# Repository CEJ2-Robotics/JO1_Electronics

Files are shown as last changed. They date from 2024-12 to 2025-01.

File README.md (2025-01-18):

# John Deere Tractor Navigation System - Electronics

<p align="justify"> This repository contains the PCB layout for a <strong>shield-style board</strong> designed to interface with the <i>NUCLEO-H745ZI-Q</i> development board. The PCB integrates various components and connection interfaces required for the tractor navigation system developed in collaboration with John Deere, serving as a practical application of embedded systems concepts. The implementation details of this electronics design can be found in the <a href="https://github.com/CEJ2-Robotics/JO1_Embedded">embedded software repository</a>.</p>

<p align="center">
  PCB 3D View
</p>

<p align="center">
  PCB Layout
</p>

## System Overview

<p align="justify">The custom PCB serves as a connection hub for the system's components, handling:</p>

<ul>
  <li><strong>Power distribution</strong> to components</li>
  <li><strong>CAN interface (FDCAN1)</strong> for encoder data</li>
  <li><strong>I2C connection (I2C4)</strong> for the MPU6050 IMU</li>
  <li><strong>SPI interface (SPI5)</strong> for the nRF24L01 wireless module</li>
  <li><strong>PWM signal routing (TIM13, TIM14, TIM1)</strong> for motors and buzzer</li>
</ul>

## Power Distribution

<p align="justify">The PCB design includes three power input screw terminals. Here's our implementation from the embedded repository:</p>

### Logic Power Screw Terminals

<ul>
  <li><strong>5V terminal:</strong> Connected to external LM2596 regulator outputting 5V</li>
  <li><strong>3.3V terminal:</strong> Connected to external LM2596 regulator outputting 3.3V</li>
  <li>Both regulators were powered by 7.4V from two <strong>3.7V Li-Po cells</strong> in series</li>
</ul>

### STM32 Power Screw Terminal

<ul>
  <li><strong>7.4V terminal:</strong> Connects directly to NUCLEO-H745ZI-Q's VIN</li>
  <li><strong>Board configuration:</strong> JP2 jumper on pins 3-4</li>
  <li><strong>Power specifications:</strong>
    <ul>
      <li><strong>Input range:</strong> 7-11V</li>
      <li><strong>Current draw varies with voltage:</strong></li>
      <ul>
        <li>800mA @ 7V</li>
        <li>450mA @ 7-9V</li>
        <li>250mA @ 9-11V</li>
      </ul>
    </ul>
  </li>
</ul>

<p align="center">
  STM32 Power Supply Input from VIN
</p>

### ESC and STM32 Connection

<ul>
  <li>The <strong>ESC</strong> is a separate pre-built circuit with its own power connections and is not powered through the PCB.</li>
  <li>In our setup, we used a <strong>7.4V Li-Po 2S battery</strong> to power both:
    <ul>
      <li>The <strong>ESC</strong> directly</li>
      <li>The <strong>STM32</strong> through the PCB's 7.4V screw terminal</li>
    </ul>
  </li>
</ul>

## Schematic Diagram & Component List

<p align="center">
  Schematic Diagram
</p>

| Component | Specifications | Purpose | Location |
|--- |--- |--- |--- |
| NUCLEO-H745ZI-Q | Dual-core ARM Cortex-M7/M4  | Main controller | Shield base board |
| Arduino Nano | ATmega328P | Encoder preprocessing | On shield PCB |
| nRF24L01 | 2.4GHz wireless module | GPS data reception | On shield PCB |
| MPU6050 | 6-DOF IMU | Orientation tracking | On shield PCB |
| GM 25-370 | 12V DC motor with encoder | Drive system | External (pins on PCB) |
| MCP2515 | CAN controller | CAN-SPI interface | On shield PCB |
| TJA1051 | CAN transceiver | CAN physical layer | On shield PCB |
| MG996R | Servo motor | Steering control | External (pins on PCB) | 
| 30A ESC | Electronic speed controller | Motor drive control | External (pins on PCB) |
| HW-508 | Passive buzzer | Audio feedback | On shield PCB |
| LM2596 (x2) | DC-DC Step Down | 5V and 3.3V regulation | External (recommended) |

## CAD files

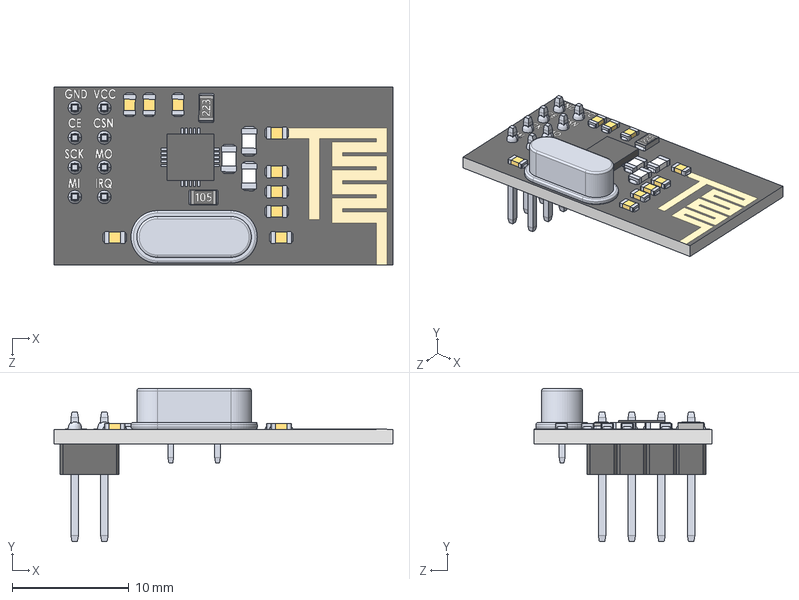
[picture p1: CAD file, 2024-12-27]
JO1_PCB/COMPONENTS/3D/NRF24L01.STEP
29.0 x 13.1 x 15.2 mm
nrfboard
CrystalOscillator
doubleMaleHeader x 4
solder x 8
1.7mmSmdCeramicCapacitor x 9
smdResistor223
smdResistor105
smdceramiccapacitorwhite x 3
4x4SMDchip

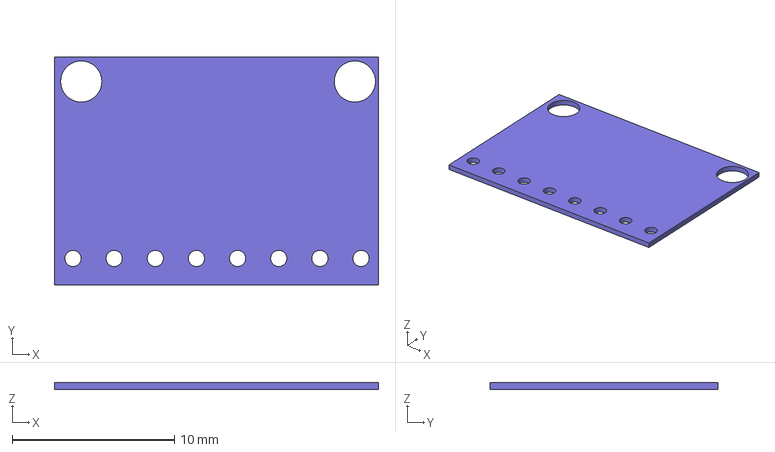
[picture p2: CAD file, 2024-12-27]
JO1_PCB/COMPONENTS/3D/TJA1051.step
20.0 x 14.1 x 0.411 mm

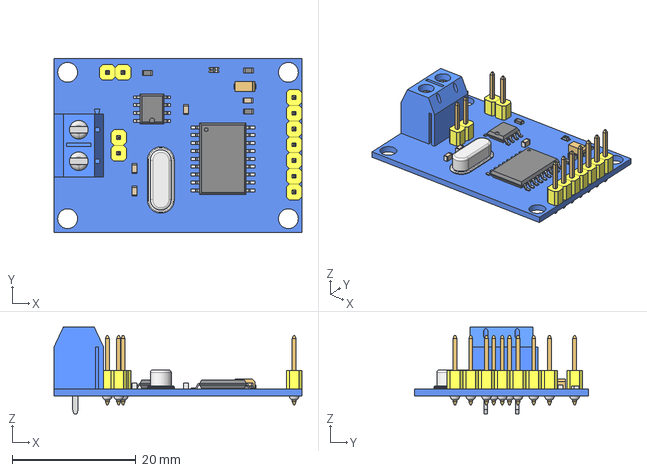
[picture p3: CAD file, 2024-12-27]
JO1_PCB/COMPONENTS/3D/MCP2515.step
40.0 x 28.0 x 14.0 mm

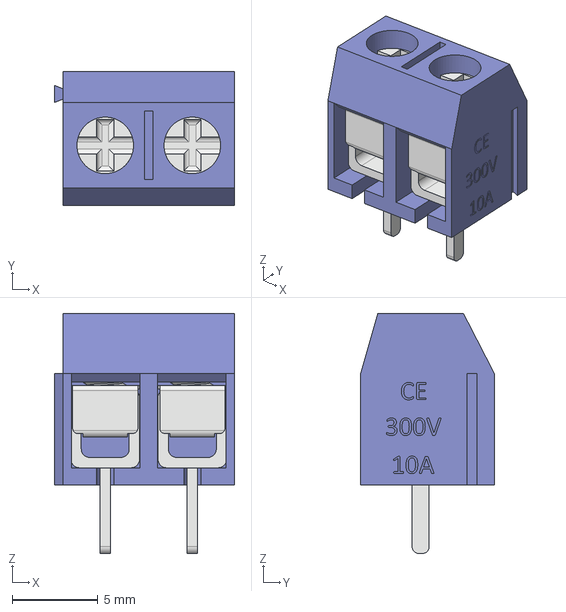
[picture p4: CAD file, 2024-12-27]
JO1_PCB/COMPONENTS/3D/SCREW_TERMINAL.step
10.5 x 7.80 x 14.0 mm

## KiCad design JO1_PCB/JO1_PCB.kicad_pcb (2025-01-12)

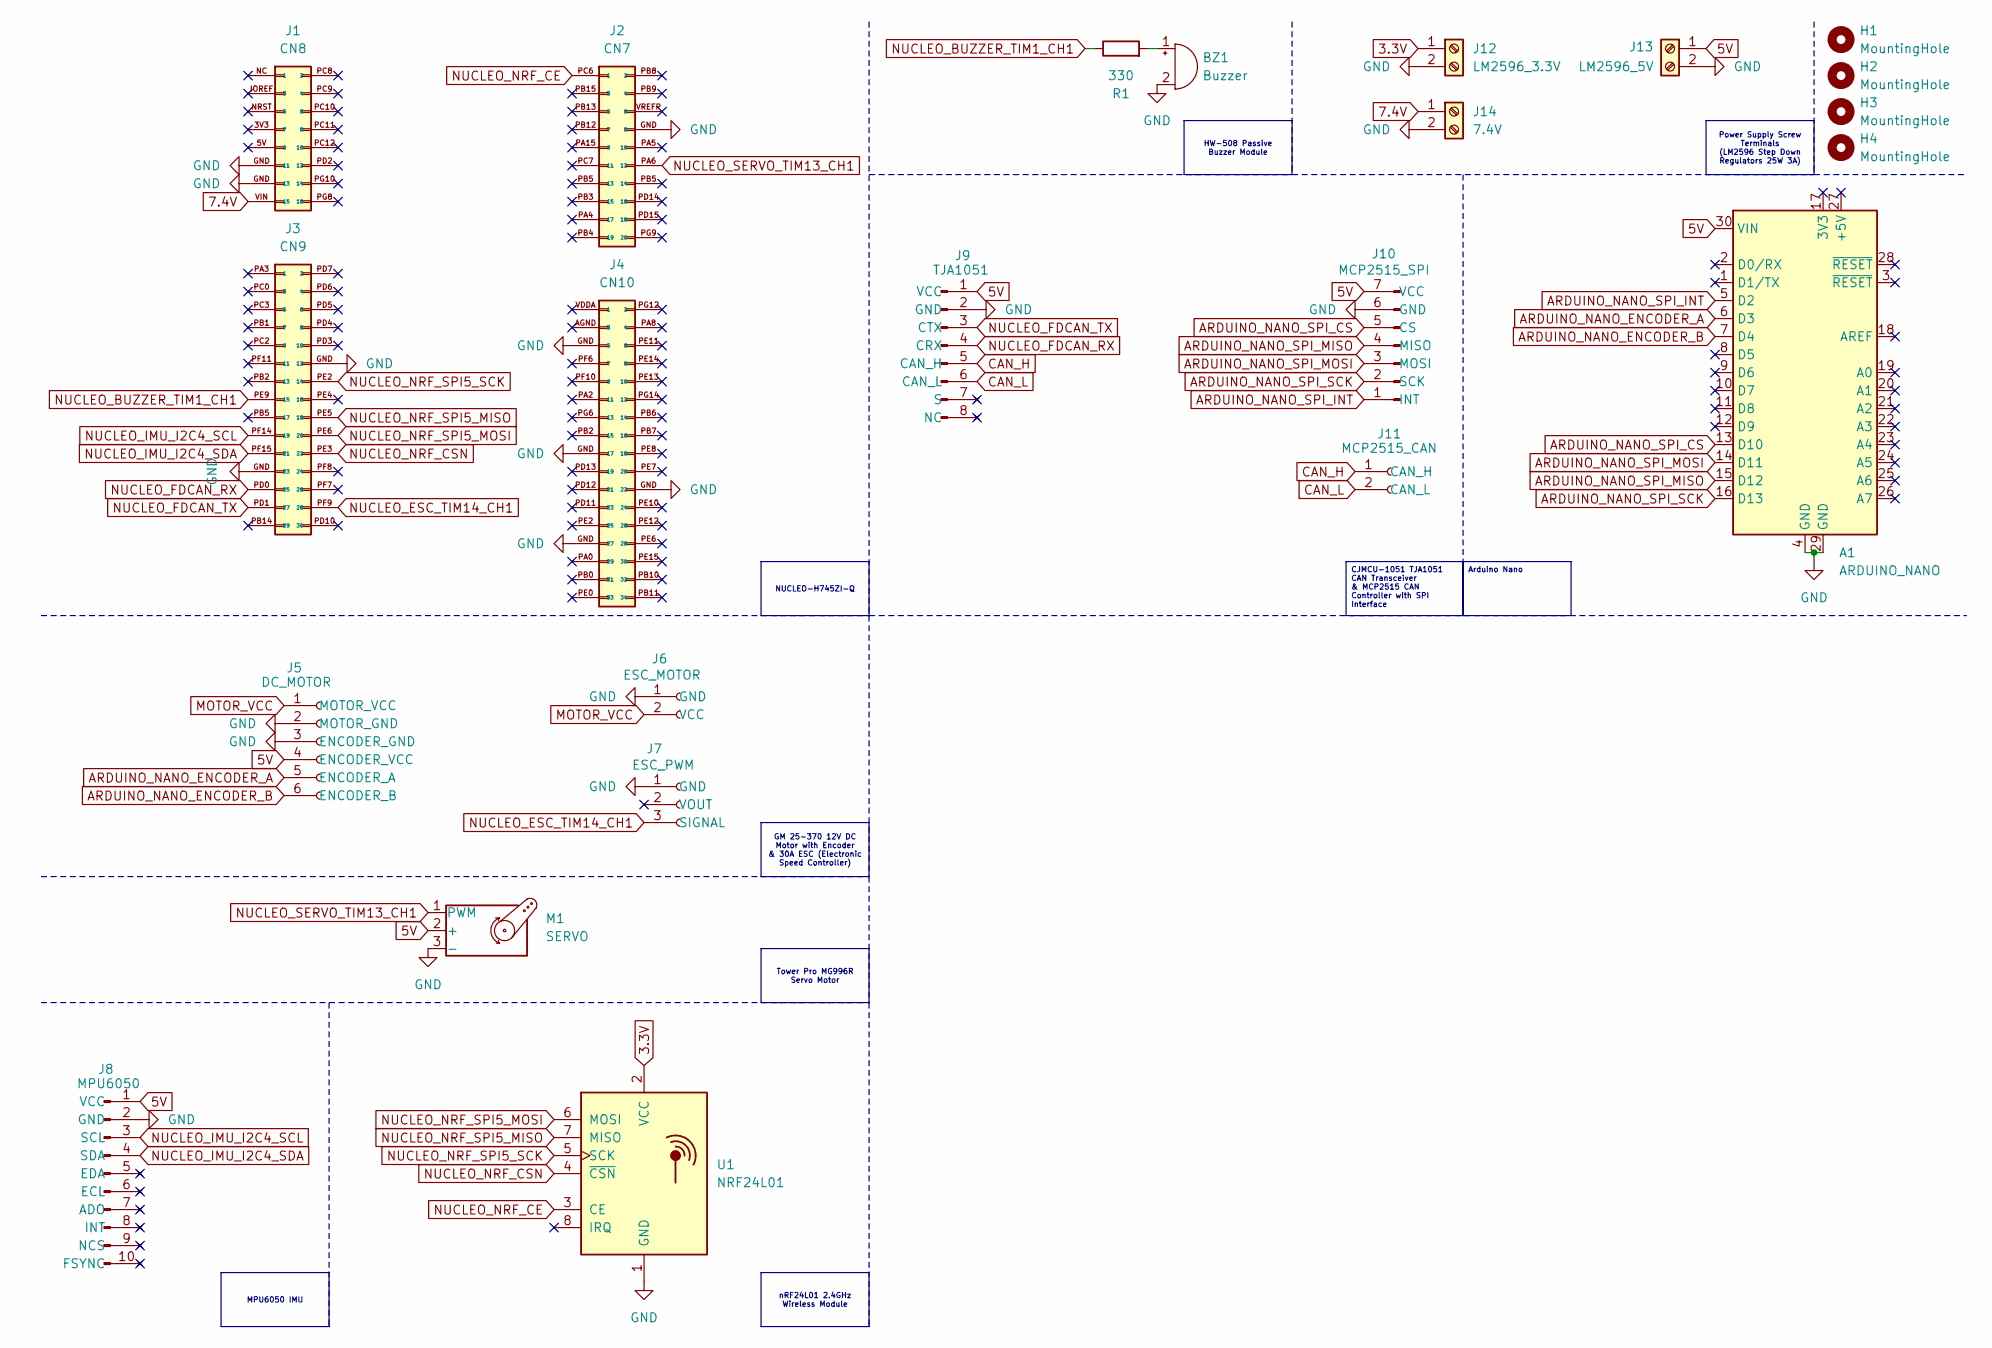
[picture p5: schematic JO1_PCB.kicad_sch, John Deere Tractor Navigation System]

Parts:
A1: ARDUINO_NANO; Arduino_Nano
BZ1: Buzzer; Buzzer_12x9.5RM7.6
H1, H2, H3, H4: MountingHole; MountingHole_2.1mm
J1: CN8; PinHeader_2x08_P2.54mm_Vertical
J2: CN7; PinHeader_2x10_P2.54mm_Vertical
J3: CN9; PinHeader_2x15_P2.54mm_Vertical
J4: CN10; PinHeader_2x17_P2.54mm_Vertical
J5: DC_MOTOR; PinHeader_1x06_P2.54mm_Vertical
J6: ESC_MOTOR; PinHeader_1x02_P2.54mm_Vertical
J7: ESC_PWM; PinHeader_1x03_P2.54mm_Vertical
J8: MPU6050; PinSocket_1x10_P2.54mm_Vertical
J9: TJA1051; PinSocket_1x08_P2.54mm_Vertical
J10: MCP2515_SPI; PinSocket_1x07_P2.54mm_Vertical
J11: MCP2515_CAN; PinHeader_1x02_P2.54mm_Vertical
J12: LM2596_3.3V; TerminalBlock_MetzConnect_Type094_RT03502HBLU_1x02_P5.00mm_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
J13: LM2596_5V; TerminalBlock_MetzConnect_Type094_RT03502HBLU_1x02_P5.00mm_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
J14: 7.4V; TerminalBlock_MetzConnect_Type094_RT03502HBLU_1x02_P5.00mm_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
M1: SERVO; PinHeader_1x03_P2.54mm_Vertical
R1: 330; R_Axial_DIN0207_L6.3mm_D2.5mm_P7.62mm_Horizontal
U1: NRF24L01; nRF24L01_Breakout

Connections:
3.3V: J12.1, U1.2 (VCC)
5V: A1.30 (VIN), J5.4 (ENCODER_VCC), J8.1 (VCC), J9.1 (VCC), J10.7 (VCC), J13.1, M1.2 (+)
7.4V: J1.VIN (15), J14.1
ARDUINO_NANO_ENCODER_A: A1.6 (D3), J5.5 (ENCODER_A)
ARDUINO_NANO_ENCODER_B: A1.7 (D4), J5.6 (ENCODER_B)
ARDUINO_NANO_SPI_CS: A1.13 (D10), J10.5 (CS)
ARDUINO_NANO_SPI_INT: A1.5 (D2), J10.1 (INT)
ARDUINO_NANO_SPI_MISO: A1.15 (D12), J10.4 (MISO)
ARDUINO_NANO_SPI_MOSI: A1.14 (D11), J10.3 (MOSI)
ARDUINO_NANO_SPI_SCK: A1.16 (D13), J10.2 (SCK)
CAN_H: J9.5 (CAN_H), J11.1 (CAN_H)
CAN_L: J9.6 (CAN_L), J11.2 (CAN_L)
GND: A1.4 (GND), A1.29 (GND), BZ1.2 (-), J1.GND (11), J2.GND (8), J3.GND (23), J4.GND (5), J5.2 (MOTOR_GND), J5.3 (ENCODER_GND), J6.1 (GND), J7.1 (GND), J8.2 (GND), J9.2 (GND), J10.6 (GND), J12.2, J13.2, J14.2, M1.3 (-), U1.1 (GND)
MOTOR_VCC: J5.1 (MOTOR_VCC), J6.2 (VCC)
NUCLEO_BUZZER_TIM1_CH1: J3.PE9 (15), R1.1
NUCLEO_ESC_TIM14_CH1: J3.PF9 (28), J7.3 (SIGNAL)
NUCLEO_FDCAN_RX: J3.PD0 (25), J9.4 (CRX)
NUCLEO_FDCAN_TX: J3.PD1 (27), J9.3 (CTX)
NUCLEO_IMU_I2C4_SCL: J3.PF14 (19), J8.3 (SCL)
NUCLEO_IMU_I2C4_SDA: J3.PF15 (21), J8.4 (SDA)
NUCLEO_NRF_CE: J2.PC6 (1), U1.3 (CE)
NUCLEO_NRF_CSN: J3.PE3 (22), U1.4 (~CSN)
NUCLEO_NRF_SPI5_MISO: J3.PE5 (18), U1.7 (MISO)
NUCLEO_NRF_SPI5_MOSI: J3.PE6 (20), U1.6 (MOSI)
NUCLEO_NRF_SPI5_SCK: J3.PE2 (14), U1.5 (SCK)
NUCLEO_SERVO_TIM13_CH1: J2.PA6 (12), M1.1 (PWM)
unnamed: BZ1.1 (+), R1.2

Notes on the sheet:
HW-508 Passive Buzzer Module
GM 25-370 12V DC Motor with Encoder & 30A ESC (Electronic Speed Controller)
Tower Pro MG996R Servo Motor
nRF24L01 2.4GHz Wireless Module
MPU6050 IMU
Power Supply Screw Terminals (LM2596 Step Down Regulators 25W 3A)
Arduino Nano
NUCLEO-H745ZI-Q
CJMCU-1051 TJA1051 CAN Transceiver & MCP2515 CAN Controller with SPI Interface

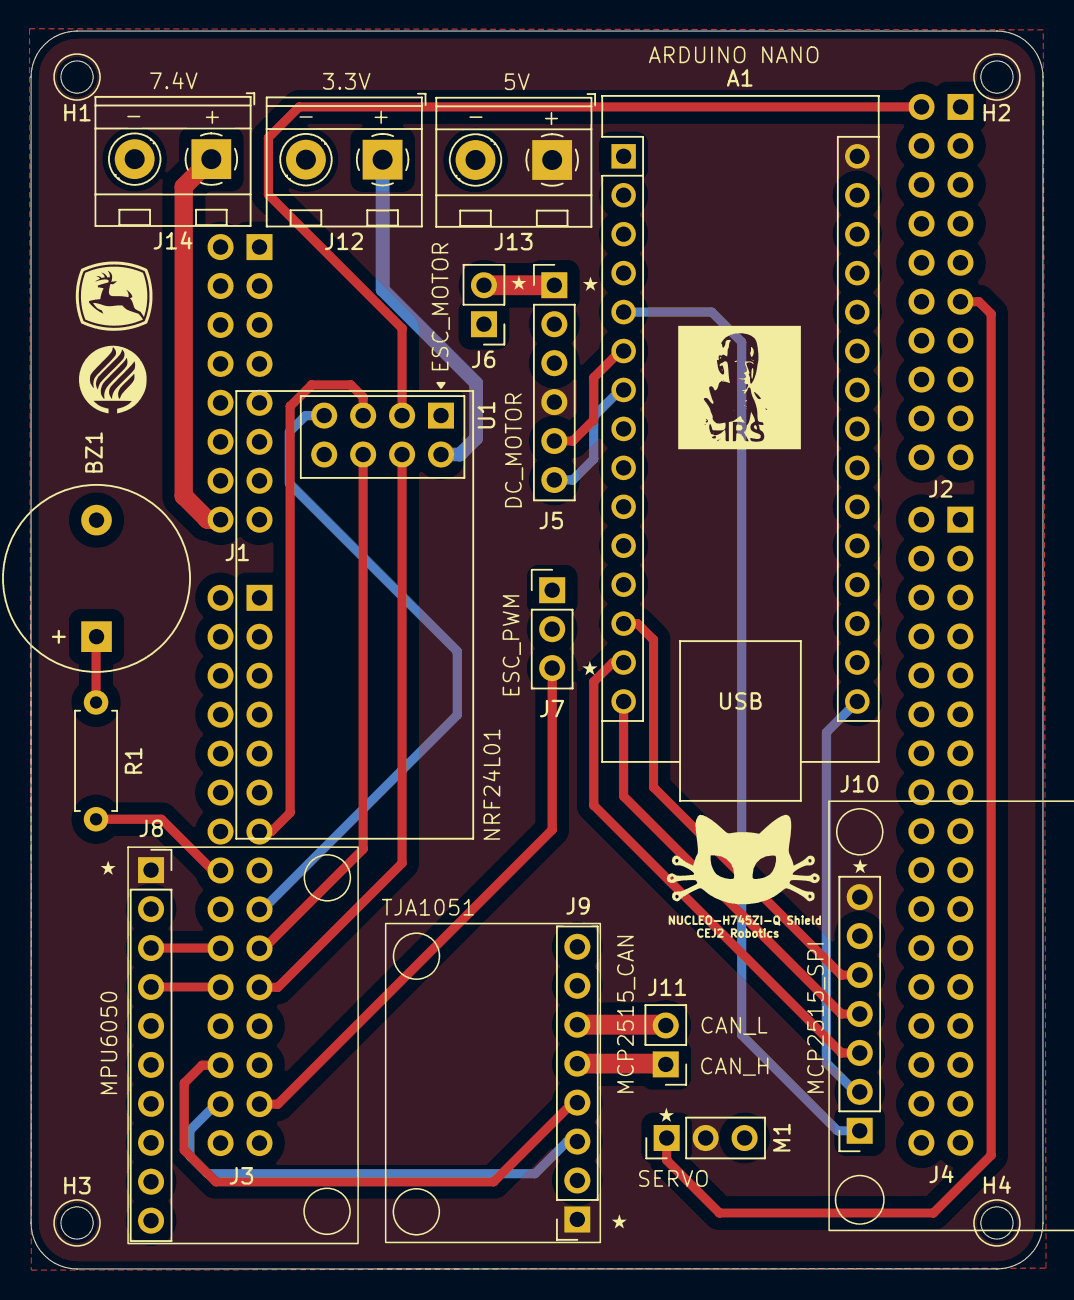
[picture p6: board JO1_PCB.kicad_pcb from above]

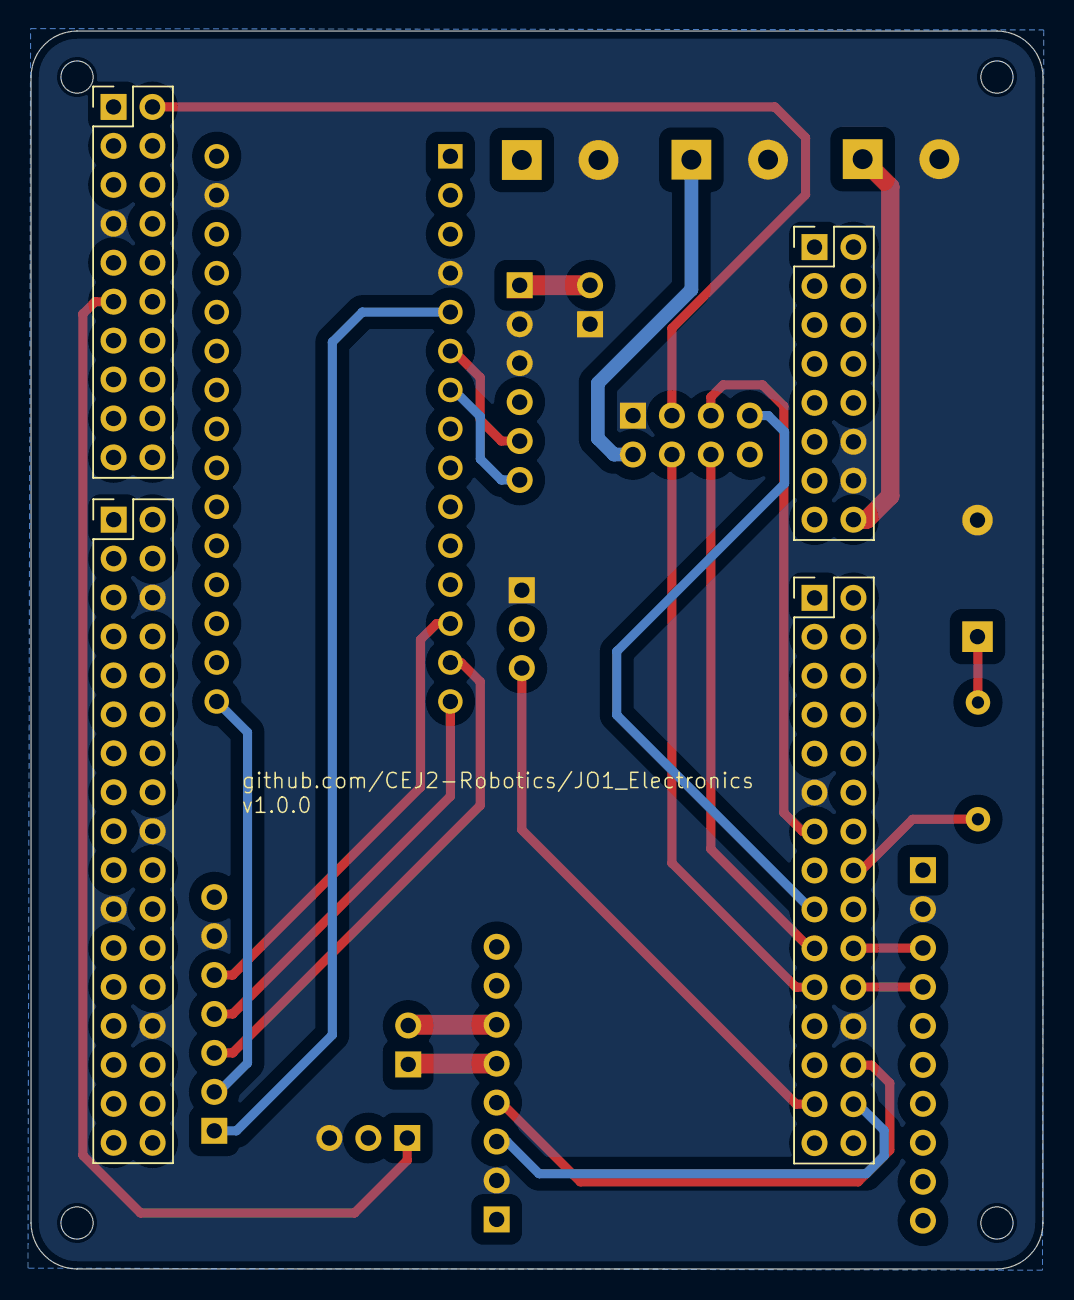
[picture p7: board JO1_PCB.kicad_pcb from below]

Board: 2 copper layers, 66.0 x 80.7 mm, 23 parts (4 on the bottom side), 27 nets.

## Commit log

2024-12-27 Final revision without routing
    [JO1_PCB.kicad_pcb, JO1_PCB.kicad_sch, MCP2515.step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]
2024-12-27 Routed PCB
    [JO1_PCB.kicad_pcb, JO1_PCB.kicad_sch]
2025-01-11 Added visual indications
    [JO1_PCB.kicad_pcb]
2025-01-12 Added text
    [JO1_PCB.kicad_pcb]
